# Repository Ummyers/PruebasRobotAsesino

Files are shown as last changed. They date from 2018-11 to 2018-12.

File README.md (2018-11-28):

## PruebasRobotAsesino
El repositorio es para las pruebas del programa final para la competencia de minisumo.

Se esta usando MSP-EXP430G2553 de la fabrica Texas Instruments

Asi como los siguientes componentes: 

1. Un regulador LD33V que convierte 5V a 3.3V el cual usa un condensador #104 (100 nanofaradios) que se conecta entre la entrada del voltaje y GND, un condensador de 10 microfaradios que va de la salida del voltaje a GND. 

2. Un regulador L7805CV que convierte 12V a 5V el cual usa un condensador #104 que va entre la salida y GND, un condensador #334 que es de 330 nanofaradios que se conecta con GND y la entrada de voltaje. 

3. Para controlar los motores usamos un driver L293D, con los pines especificados de la siguiente manera:
   Pines de entrada 2,7,15,10.\\
   Pines de salida 3,6,14,11.
ETC...

Algunas especificaciones del MSP:

El pin 1 es VCC que debe recibir a lo mas 3.3 Volts del pin 1 al 16 va un condensador de 1 nanoFaradio, del pin 16 al 20, una resistencia de 47K.

La fuente inicialmente era de 12V usamos los reguladores para obtener 5 y 3.3 volts.

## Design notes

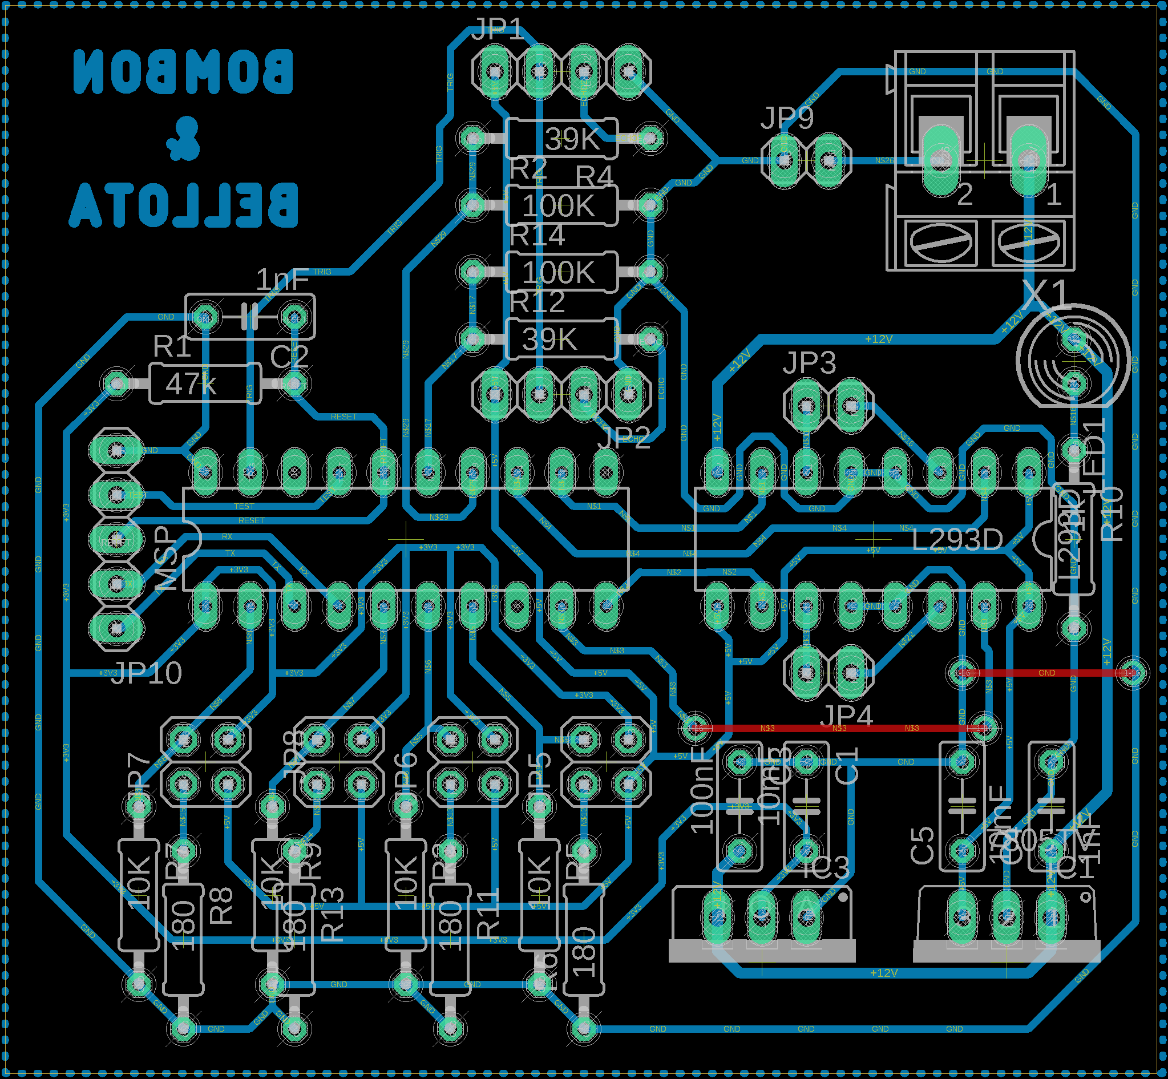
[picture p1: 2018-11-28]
BRDCircuitoRobotASESINO.png

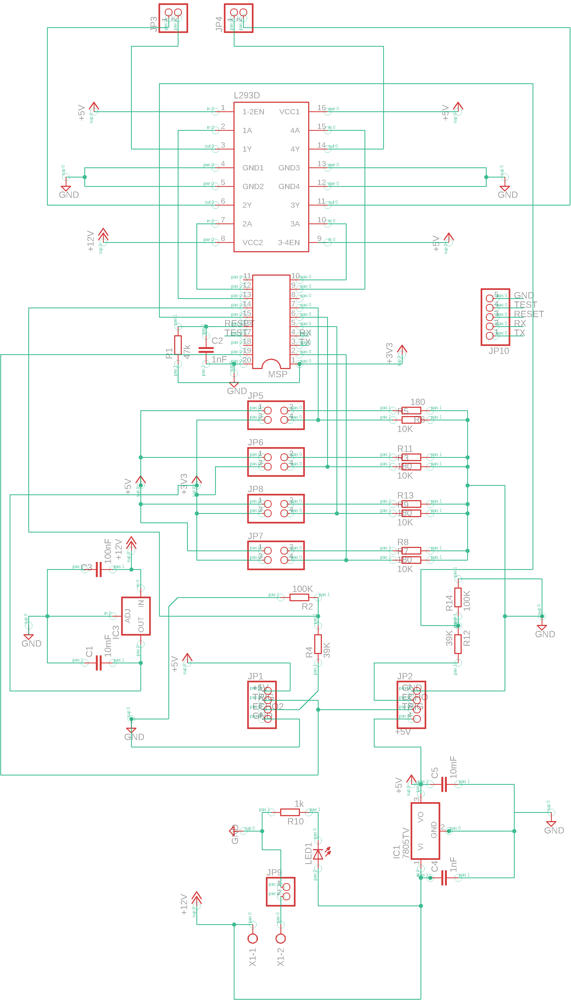
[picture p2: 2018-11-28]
EsquematicoCircuitoROBOTASESINO.png

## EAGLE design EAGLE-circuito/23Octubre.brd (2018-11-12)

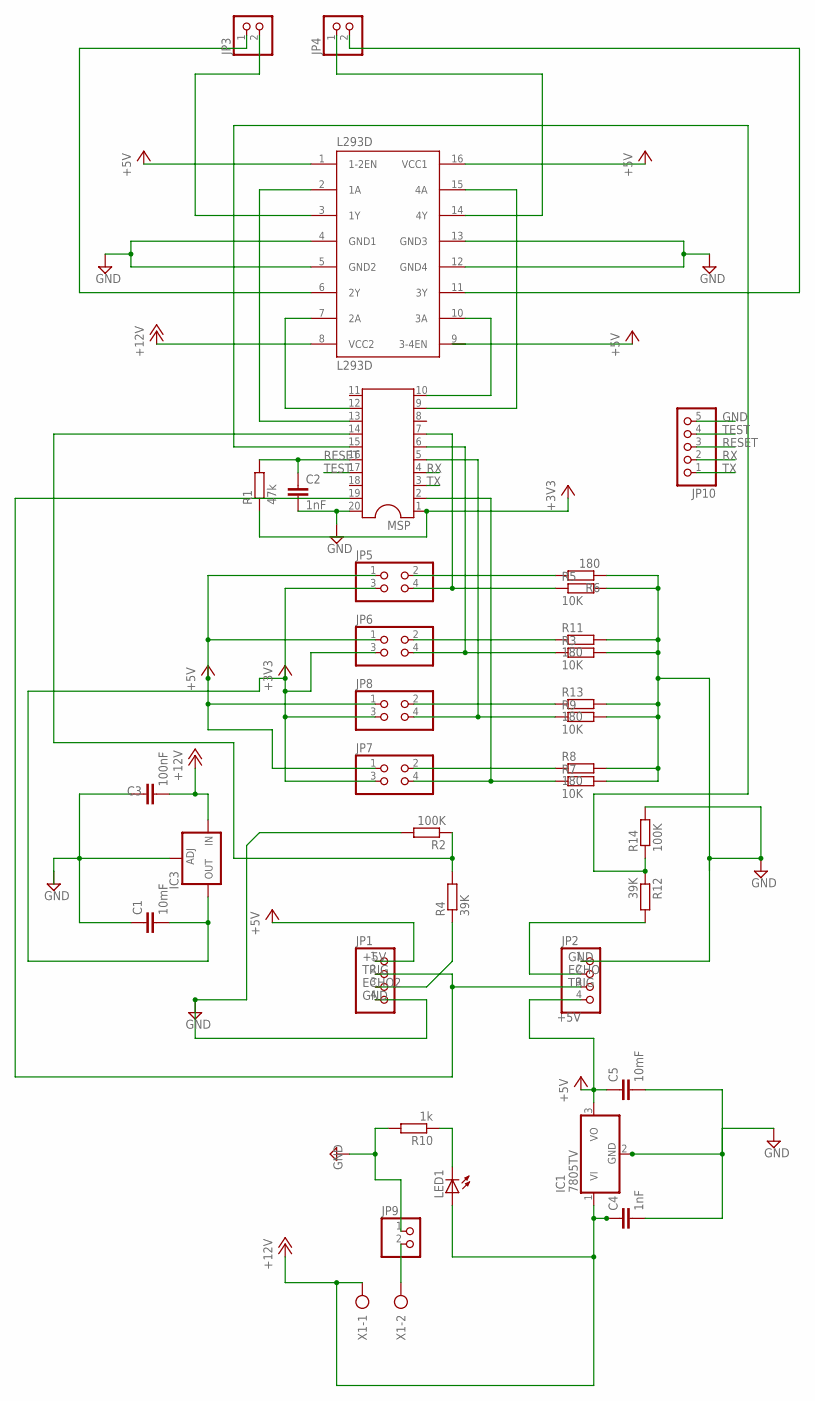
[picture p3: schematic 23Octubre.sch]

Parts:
C1, C5: 10mF; C050-025X075
C2, C4: 1nF; C050-025X075
C3: 100nF; C050-025X075
IC1: 7805TV; TO220V
IC3: LM317TS; 317TS
JP1, JP2: PINHD-1X4; 1X04
JP3, JP4, JP9: PINHD-1X2; 1X02
JP5, JP6, JP7, JP8: PINHD-2X2; 2X02
JP10: PINHD-1X5; 1X05
L293D: L293D; DIL16
LED1: LED5MM
MSP: DIL20
R1: 47k; 0207/10
R2, R14: 100K; 0207/10
R3, R5, R7, R9: 10K; 0207/10
R4, R12: 39K; 0207/10
R6, R8, R11, R13: 180; 0207/10
R10: 1k; 0207/10
X1: AK300/2

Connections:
+3V3: C1.2, IC3.2 (OUT), JP5.3, JP6.3, JP7.3, JP8.3, MSP.1, R1.1
+5V: C5.1, IC1.3 (VO), JP1.1, JP2.4, JP5.1, JP6.1, JP7.1, JP8.1, L293D.1 (1-2EN), L293D.9 (3-4EN), L293D.16 (VCC1)
+12V: C3.2, C4.1, IC1.1 (VI), IC3.3 (IN), L293D.8 (VCC2), LED1.A, X1.1
ECHO: JP2.2, R12.2
ECHO2: JP1.3, R4.1
GND: C1.1, C2.2, C3.1, C4.2, C5.2, IC1.2 (GND), IC3.1 (ADJ), JP1.4, JP2.1, JP9.1, JP10.5, L293D.4 (GND1), L293D.5 (GND2), L293D.12 (GND4), L293D.13 (GND3), MSP.20, R2.2, R3.2, R5.2, R6.1, R7.2, R8.2, R9.2, R10.2, R11.2, R13.2, R14.2
unnamed: L293D.7 (2A), MSP.12
unnamed: L293D.10 (3A), MSP.10
unnamed: L293D.15 (4A), MSP.9
unnamed: L293D.2 (1A), MSP.13
unnamed: JP5.4, MSP.7, R5.1
unnamed: JP6.4, MSP.6, R3.1
unnamed: JP8.4, MSP.5, R9.1
unnamed: JP7.4, MSP.2, R7.1
unnamed: JP3.1, L293D.6 (2Y)
unnamed: JP5.2, R6.2
unnamed: JP6.2, R11.1
unnamed: JP8.2, R13.1
unnamed: JP7.2, R8.1
unnamed: JP3.2, L293D.3 (1Y)
unnamed: MSP.15, R12.1, R14.1
unnamed: LED1.K (C), R10.1
unnamed: JP4.2, L293D.11 (3Y)
unnamed: JP4.1, L293D.14 (4Y)
unnamed: JP9.2, X1.2
unnamed: MSP.14, R2.1, R4.2
RESET: C2.1, JP10.3, MSP.16, R1.2
RX: JP10.2, MSP.4
TEST: JP10.4, MSP.17
TRIG: JP1.2, JP2.3, MSP.19
TX: JP10.1, MSP.3

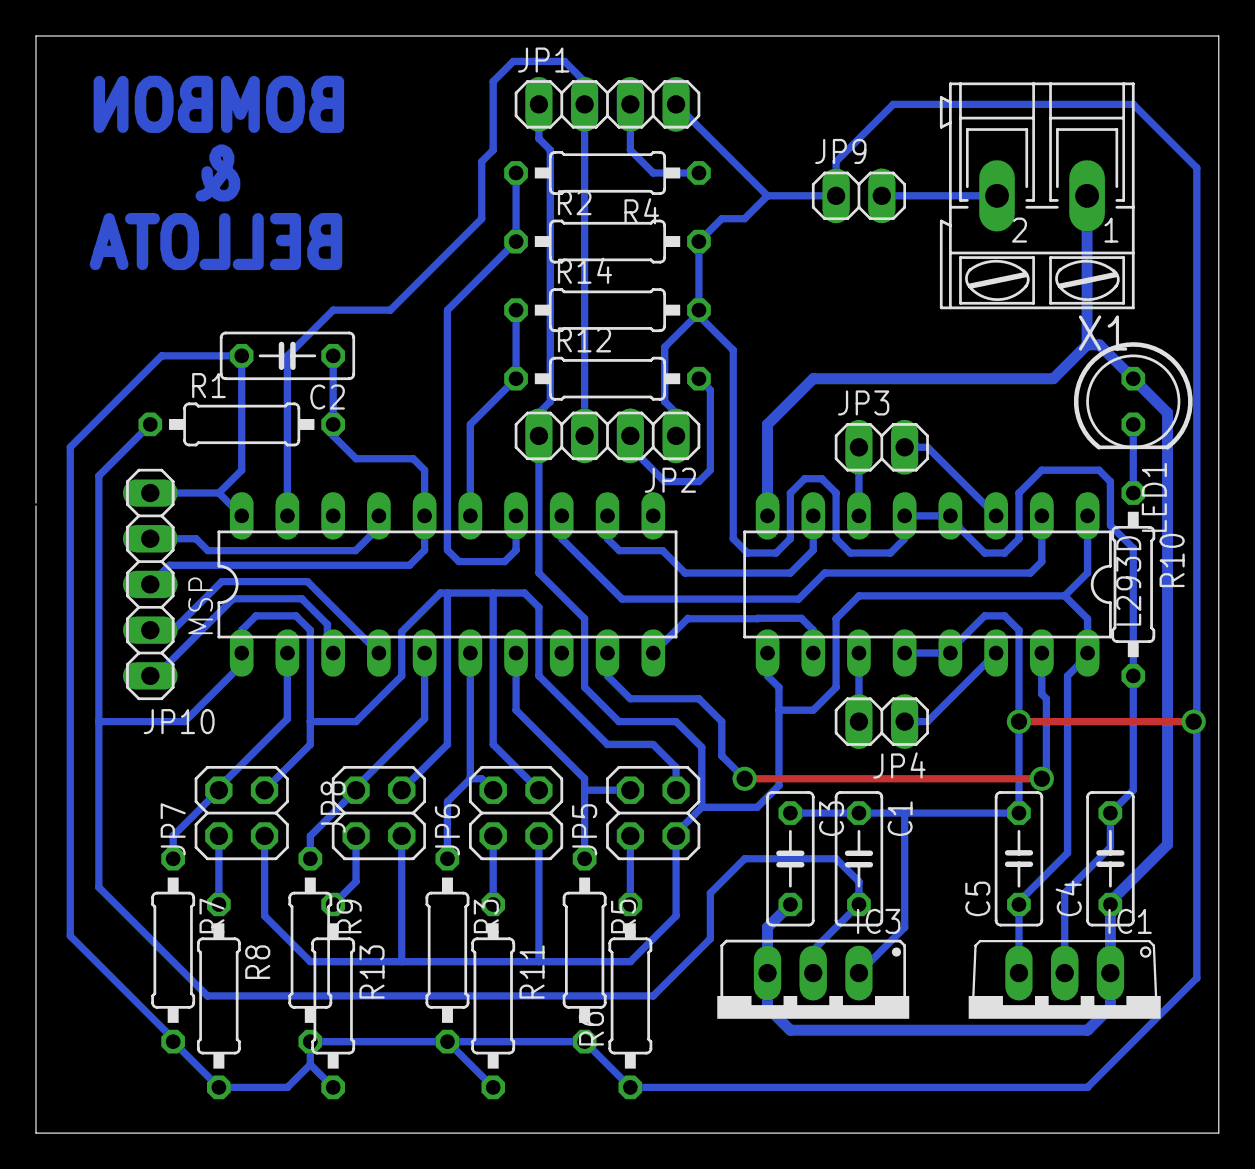
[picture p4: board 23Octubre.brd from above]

Board: 2 copper layers, 65.7 x 61.0 mm, 35 parts (0 on the bottom side), 31 nets.

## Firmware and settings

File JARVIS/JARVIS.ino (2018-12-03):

/* Facultad de Ciencias, UNAM
 *  @Autor Muñiz Patiño, Andrea Fernanda
 *  @Fecha 29/Noviembre/2018
 *  @versión FINAL
 *  COmpetencia de Robótica
 */
 //------------PINES-------------

//------------SONARES-----------
//La salida del trigger es la misma para los dos sonares.
#define TRIGGER 19 
//Sonar localizado en el frente
#define ECHO 14

//---------INFRARROJOS------------
//Infrarrojo Arriba BETA
#define infraArriba 5
//Infrarrojo Abajo GAMMA
#define infraAbajo  2
//Infrarrojo Cental ALFA
#define infraCentral 7

//-----------MOTORES---------------
//Arriba 
#define motor_p12 12
#define motor_p13 13
//Abajo en la placa 
#define motor_p9 9
#define motor_p10 10
//NOTA: Consultar EAGLE para dudas y aclaraciones

//-------Variables-------------
//Variable para calcular la distancia del robot enemigo
const float sonido = 34300.0;
int valueI = 120;
int valueGiroI = 120;
int valueGiroLLI = 250;

int valueGiro = 120;
int valueGiroLL = 250;
int valueAsesinar = 250;

int tiempoTornado = 0;

// Variables para la calibración
//float minAr = 1023.0;
//float maxAr = 0.0;

float minAb = 1023.0; 
float minC = 1023.0; 
float maxAb = 0.0; 
float maxC = 0.0;
float sensorValueAr, sensorValueAb, sensorValueC; 

float sensorArriba, sensorAbajo, sensorCentral;

void setup() {
  //Serial.begin(9600);
  pinMode(motor_p12, OUTPUT);  
  pinMode(motor_p13, OUTPUT);
  pinMode(motor_p9, OUTPUT);
  pinMode(motor_p10, OUTPUT);  
  
  pinMode(TRIGGER, OUTPUT);
  pinMode(ECHO, INPUT);

  pinMode(infraArriba, INPUT);
  pinMode(infraAbajo, INPUT);
  pinMode(infraCentral, INPUT);
  while (millis() < 2500) {
      calibrar();
    }//END Millis WHILE
    
    //-------------INCERTIDUMBRE
    // 01:03 se modifica a 3% la incertidumbre
    // 02:42 se modifica a 5% la incertidumbre, pinshe negro
 // maxAr = maxAr + (maxAr * .05);
  maxAb = maxAb + (maxAb * .05);
  maxC = maxC + (maxC * .05);
  
     /*
      * 
  Serial.println("Sensor Arriba");
  Serial.println(minAr);
  Serial.println(maxAr);
  Serial.println("Sensor Abajo");
  Serial.println(minAb);
  Serial.println(maxAb);
  Serial.println("Sensor Central");
  Serial.println(minC);  
  Serial.println(maxC);
  Serial.println("-----------------");
  delay(1000);
      */
}

void loop() {

  sensorArriba = analogRead(infraArriba);
  sensorAbajo = analogRead(infraAbajo);

  if((sensorAbajo > minAb)&&(sensorAbajo < maxAb)){ 
      //Serial.println("entro al primer if");
      iniciarTrigger();  
    //Si tenemos pegado el robot empujar lo mas que se pueda
    float distanciaFrente = calcularDistanciaFrente();
    //El siguiente if es para cuando el robot esta demasiado cerca
   if((distanciaFrente >= 2.00)&&(distanciaFrente < 33.00)){
          empujar(true); 
      }else{
        girar();
        tiempoTornado++;
        if(tiempoTornado >= 300){
          analogWrite(motor_p13, 80);
          analogWrite(motor_p12, 0);
          analogWrite(motor_p9, 80); 
          analogWrite(motor_p10, 0);
          tiempoTornado = 0;
        }
      }
    }else{ 
      //Retrocede y luego gira, para no caer xD supuestamente
      //Serial.println("entro al else"); 
     analogWrite(motor_p13, valueI);
     analogWrite(motor_p12, 0);
     analogWrite(motor_p9, valueI); 
     analogWrite(motor_p10, 0);
     
     analogWrite(motor_p13, 0);
     analogWrite(motor_p12, valueGiroLLI);
     analogWrite(motor_p9, valueGiroI);
     analogWrite(motor_p10, 0);
    }
  
}//END LOOP

//----------------METODOS AUXILIARES-------------------------
/* Método que intenta sacar al enemigo de la pista, aumentando la velocidad
 * @param boolean direccion
 * TRUE empuja hacia adelante
 * FALSE empuja hacia atrás
*/
 void empujar(boolean direccion){
  int a = 0;
  int b = 0;
  if(direccion){
    b = valueAsesinar;
  }else{
    a = valueAsesinar;
  }
    analogWrite(motor_p12, a);
    analogWrite(motor_p13, b);
    
    analogWrite(motor_p9, a);
    analogWrite(motor_p10, b);
    delay(100);
    analogWrite(motor_p12, a);
    analogWrite(motor_p13, b);
    
    analogWrite(motor_p9, a);
    analogWrite(motor_p10, b);
    
    
}//END empujar

/* Método GIRAR derecha/izquierda
*/
  void girar(){
      analogWrite(motor_p12, valueGiroLL);
      analogWrite(motor_p13, 0);  
          
      analogWrite(motor_p9, 0);
      analogWrite(motor_p10, valueGiro);  
      //delay(300);
      //En vez de poner delay, hay que regular la velocidad
}//END girar

void calibrar(){
      //-------------SENSOR ABAJO--------------------
      sensorValueAb = analogRead(infraAbajo);     
       if (sensorValueAb > maxAb) {
        maxAb = sensorValueAb;
      }      
      // Registrar el valor mínimo del sensor
      if (sensorValueAb < minAb) {
        minAb = sensorValueAb;
      }
      //------------SENSOR CENTRAL-------------------
      int sensorValueC = analogRead(infraCentral);
      if (sensorValueC > maxC) {
        maxC = sensorValueC;
      }      
      // Registrar el valor mínimo del sensor
      if (sensorValueC < minC) {
        minC = sensorValueC;
      }
}//END calibrar

/*Devuelve un float que es el valor de la distancia de un objeto con respecto al robot
 * ----------------------------------------------------------------------------------
 */
float calcularDistanciaFrente(){
  // La función pulseIn obtiene el tiempo que tarda en cambiar entre estados, en este caso a HIGH
  unsigned long tiempo = pulseIn(ECHO, HIGH ); 
  // Obtenemos la distancia en cm, hay que convertir el tiempo en segudos ya que está en microsegundos
  // por eso se multiplica por 0.000001
  float distancia = tiempo * 0.000001 * sonido / 2.0;
  return distancia;
}
/*Metodo que inicia la secuencia del sonar
 * --------------------------------------------------
*/
void iniciarTrigger()
{
  // Ponemos el Trigger en estado bajo y esperamos 2 ms
  digitalWrite(TRIGGER, 0);
  delayMicroseconds(2);
  // Ponemos el pin Trigger a estado alto y esperamos 10 ms
  digitalWrite(TRIGGER, 1);
  delayMicroseconds(10);
  // Comenzamos poniendo el pin Trigger en estado bajo
  digitalWrite(TRIGGER, 0);
}//END iniciarTrigger

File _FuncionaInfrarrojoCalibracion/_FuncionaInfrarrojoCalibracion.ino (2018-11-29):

/*  Facultad de Ciencias, UNAM
 *  @Autor Muñiz Patiño, Andrea Fernanda
 *  @Fecha 27/Novimebre/2018
 *  @versión 3.0
 *   
 *   12:30 am Funciona este programa para que se mantenga en una zona
 *   de un mismo color
 * 
 * Esquema del ROBOT
 *                      LLANTA 
 * ---------------------------
 * - beta                    -
 * -                         -
 * -                         -
 * -                       alfa
 * -                         -
 * -                         -
 * - gamma                   -
 * ---------------------------
 *                      LLANTA
 * 
 * 
 */
//Probando los infrarrojos
#define motor_p9 9
#define motor_p10 10
#define motor_p12 12
#define motor_p13 13

//---------INFRARROJOS------------
//Infrarrojo Arriba BETA
#define infraArriba 5
//Infrarrojo Abajo GAMMA
#define infraAbajo  2
//Infrarrojo Cental ALFA
#define infraCentral 7

//-----------VARIABLES-------------
//Se usaran cuando pasemos a PWD para la velocidad de los motores
int value = 120;
int valueGiro = 250;
int valueGiroLL = 200;
int valueAsesinar = 250;

// Variables para la calibración
float minAr = 1023.0;
float minAb = 1023.0; 
float minC = 1023.0; 
float maxAr = 0.0;
float maxAb = 0.0; 
float maxC = 0.0;
float sensorValueAr, sensorValueAb, sensorValueC; 

float sensorArriba, sensorAbajo, sensorCentral;

//-------------------SETUP------------------------
void setup() {
  pinMode(motor_p9, OUTPUT);
  pinMode(motor_p10, OUTPUT); 
  pinMode(motor_p12, OUTPUT);
  pinMode(motor_p13, OUTPUT); 

  pinMode(infraArriba, INPUT);
  pinMode(infraAbajo, INPUT);
  pinMode(infraCentral, INPUT); 
  while (millis() < 4000) {
      calibrar();
    }//END Millis WHILE
    //-------------INCERTIDUMBRE
  maxAr = maxAr + (maxAr * .05);
  maxAb = maxAb + (maxAb * .05);
  maxC = maxC + (maxC * .05);
    Serial.begin(9600);
}

void loop() {
  /*Comunicación Serial
   *  Serial.println("Sensor Arriba");
  Serial.println(minAr);
  Serial.println(maxAr);
  Serial.println("Sensor Abajo");
  Serial.println(minAb);
  Serial.println(maxAb);
  Serial.println("Sensor Central");
  Serial.println(minC);  
  Serial.println(maxC);
  delay(1000);
  
  sensorCentral = analogRead(infraCentral);
    if(sensorCentral > maxC){ 
       analogWrite(motor_p13, value);//ET
       analogWrite(motor_p12, 0);
       analogWrite(motor_p9, 0);
       analogWrite(motor_p10, value);//ET
    }
    //GIRA Y LUEGO RETROCEDE
   */
  sensorArriba = analogRead(infraArriba);
  sensorAbajo = analogRead(infraAbajo);
  
  if((sensorArriba > minAr)&&(sensorArriba < maxAr)&&(sensorAbajo > minAb)&&(sensorAbajo < maxAb)){  
   analogWrite(motor_p13, value);//ET
   analogWrite(motor_p12, 0);
   analogWrite(motor_p9, 0);
   analogWrite(motor_p10, value);//ET
  }else{ 
//Intentando dar vuelta sin un motor
   analogWrite(motor_p13, 0);
   analogWrite(motor_p12, 0);
   analogWrite(motor_p9, valueGiro);
   analogWrite(motor_p10, 0);

   analogWrite(motor_p13, value);
   analogWrite(motor_p12, 0);
   analogWrite(motor_p9, value);
   analogWrite(motor_p10, 0);
   
  }
}//END LOOP

//----------------METODOS AUXILIARES-------------------------

void calibrar(){
//---------------SENSOR ARRIBA----------------
      //Leer lo que el sensor arroje
      sensorValueAr = analogRead(infraArriba);
      // Registrar el valor máximo del sensor
      if (sensorValueAr > maxAr) {
        maxAr = sensorValueAr;
      }      
      // Registrar el valor mínimo del sensor
      if (sensorValueAr < minAr) {
        minAr = sensorValueAr;
      }
      //-------------SENSOR ABAJO--------------------
      sensorValueAb = analogRead(infraAbajo);     
       if (sensorValueAb > maxAb) {
        maxAb = sensorValueAb;
      }      
      // Registrar el valor mínimo del sensor
      if (sensorValueAb < minAb) {
        minAb = sensorValueAb;
      }
      //------------SENSOR CENTRAL-------------------
      int sensorValueC = analogRead(infraCentral);
      if (sensorValueC > maxC) {
        maxC = sensorValueC;
      }      
      // Registrar el valor mínimo del sensor
      if (sensorValueC < minC) {
        minC = sensorValueC;
      }
}

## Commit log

2018-11-08 Pruebas de vuelo segundo dia
    Pruebas del primer día y segundo día, se calibro la velocidad de los motores.
2018-11-10 Update _8NovPrueba1/_8NovPrueba1.ino
    Se borro el ultimo digitalWrite del metodo iniciarTrigger por que la variable tiempo nos devolvia 0, pero el problema fue que había una pista discontinua en el circuito impreso
2018-11-11 Mueve motores
    Atrás, adelante, giro.
2018-11-11 Base de datos
    Para ver archivos
2018-11-12 Eagle archivos
    Se agregan los archivos de eagle, circuito impreso
    [23Octubre.brd, 23Octubre.sch]
2018-11-15 Se agrego el delay
    Se agrego el delay para el inicio de la competencia sin embargo no se pudieron hacer las pruebas necesarias por un regulador.
2018-11-23 Un buen de pruebas
2018-11-28 PAra que el sketch sirva
2018-11-28 actualizaciones de la semana pasada
2018-11-28 Imagenes del circuito EAGLE
2018-11-29 15HRS antes de la competencia
2018-12-03 Actualizacion de tiempo
